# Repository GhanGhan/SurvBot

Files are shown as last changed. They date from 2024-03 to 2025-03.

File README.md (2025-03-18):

# SurvBot
Remote controlled robot that surveys the environment it is travelling in.  Designed in KiCad and Altium Designer.

# Part One - Robot Control Unit (RCU)
***Figure 1: Altium Designer 3D View***
3d View

***Figure 2: KiCad 3D View***
Full3D

## Block Diagaram
***Figure 3: SYSTEM BLOCK DIAGRAM (SIMPLE)***

Block_Diagram2

## Project Overview
- Design and implement a PCB that has closed-loop control over 2 DC motors
- Monitors and saves data about itself and the environment it is in:
  - Current flowing though the motors
  - Ambient temperature
  - Ambient light hitting the robot
  - Humidity
  - Orientation (or just the tilt angle, TBD)
- Possess Bluetooth communication
- Entire system is powered by a 9V-12V battery

***Figure 4: SYSTEM OVERVIEW***
Overview

## Schematic Diagrams
### Power
***Figure 5: Power Schematic***
Power 1
- Can be connected to a < 20V at the battery terminals, as well as 5V at either USB connector
- Schottky diodes allow for all three power sources to be connected at once
  - Battery terminal has the highest priority, followed by USB1, then USB2
  - They also provide reverse voltage protection
- Battery can power all of the modules, USB1 and USB2 power all modules except the motor control module
- U100 provides 6V with a maximum output of 3A
- U101 provides 3.3V with a maximum output of 2A
- U102 provides 3.3VA with a maximum output of 1.35A

### Microconroller
***Figure 6: Microconroller Schematic***
Microcontroller 2
- Powered by 3.3V
- Using STM32G0B1CBT6 microcontroller with a clock speed of 16MHz
- Using SWD Interface to program and debug
- Communicates to peripheral ICs using I2C, UART and SPI
- Can use PWM or PH/EN protocol to control motors
- Can connect to a host computer via the USB interface

### Motor Control
***Figure 7: Motor Control Schematic***
Motor_Control 3
- Powered by 6V
- The DRV8876 driver, one for each motor, takes control input signals form microcontroller
- Each motor driver can draw up to 1.5A before shutting down
- Each driver outputs current proportional to the current passing through its associated motor, which is converted to a voltage and sent to a voltage buffer
- Each motor has quadrature encoders, whose signals are fed to the microcontroller

### Bluetooth
***Figure 8: Bluetooth Schematic***
Bluetooth 4
- Powered by 3.3V
- Using ESP32-Mini as a UART-Bluetooth bridge to communicate with a remote controller
- Can be programmed using USB 2.0 via the USB-to-UART IC: CH340C
- By sliding a SPDT switch, can switch between programming mode and communication mode

### Sensors
***Figure 9: Sensors Schematic***
Sensors 5
- Powered by 3.3V
- Communicate with microcontroller via I2C interface
- APDS-9306-065: Ambient light sensor, automatically rejects 60Hz flicker
- SHT3D-DIS: Temperature and humidity sensor
- LSM6D53: 6-axis accelerometer and gyroscope

### Current Feedback
***Figure 10: Current Feedback Schematic***
Current_FDB 6
- Powered by 3.3VA
- Takes buffered current-sense output of left and right motor driver as input
  - Signals are filtered to attenuate switching noise before entering the buffer
- Using ADC121C02CIMK to convert analog signal to 12bit digital signal
- Communicates with microcontroller via I2C

### External Memory
***Figure 11: External Memory Schematic***
External_Memory 7
- Powered by 3.3V
- 32Mb NOR Flash memory
- Communicates with microcontroller via SPI

# Part Two - Remote Controller
***Figure 12: 3D View***
3D View Front

Battery powered hand-held device that controls and monitors the state of the SurvBot. Commands are sent and data is received over Bluetooth. The design includes joysticks to control the robot’s velocity, buttons to change the mode it is in and a screen to display the sensor data. Can be used outdoors or indoors.

## Project Overview
***Figure 13: Remote controller Bloack Diagram***
Block Diagram
The user interface will contain joysticks and buttons to control the robot’s velocity and the state it is in.   Such states will determine whether the robot responds to velocity inputs, recording sensor data, is in low power mode etc.  Velocity commands and state changes are sent from the controller to the robot via Bluetooth.  The controller will receive sensor data; encoders, temperature, humidity and motor current from the robot in and display it on the onboard screen in real time.
The system will:
- be powered by a 9V battery
- use 2 thumb joysticks, one to control the robot’s linear velocity and another to control it’s angular velocity
- provide a USB interface to to program the microcontroller
- communicate with the SurvBot over Bluetooth
- provide a screen to view the data from the SurvBot’s motion and environment sensors, and Bluetooth connection status

## Schematic Diagrams
### Power
***Figure 14: Power Schematic***
Power
- Primary power source is a rechargeable 9V battery
- Secondary power source is a USB vable
- Power multiplexing circuitry used to decide the power source
- Power Rails 3.3V and 3V (for the LCD screen)

### Microcontroller
***Figure 7: Microconroller Schematic***
uC and BT
- Programmed via a USB cable whose signals are converted to UART
- Peripherals: ADC, SPI and GPIO
- Has integrated Bluetooth antenna

### User Interface
***Figure 7: User Interface: Screen, Buttons, and Joysticks***
User Interface
- LCD screen displays information such as state of Bluetooth connection, current speed, temperature, recorded data etc.
- Features 8 buttons to control the state of the robot
- Left joysticks controls rotational speed, right joystick controls linear speed

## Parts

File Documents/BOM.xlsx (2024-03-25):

Part Name | Details/Purpose | Price | Quantity | Cost | Link | Datasheet
ROB-17279 | 2-Level, 2-wheel Robot Chassis | $16.50 | 1 | $16.50 | https://www.digikey.ca/en/products/detail/sparkfun-electronics/ROB-17279/13677596 | https://mm.digikey.com/Volume0/opasdata/d220001/medias/docus/3604/Assembly_Guide_for_SparkFun_JetBot_AI_Kit_V2.0_Web.pdf
FIT0458 | GEARMOTOR 160 RPM 6V W/ ENCODER | $7.40 | 2 | $14.80 | https://www.digikey.ca/en/products/detail/dfrobot/FIT0458/7087167 | https://mm.digikey.com/Volume0/opasdata/d220001/medias/docus/5786/FIT0458.pdf
105090004 | MAKER MDD3A - DUAL CHANNEL 3A DC (Motor Driver) | $6.90 | 1 | $6.90 | https://www.digikey.ca/en/products/detail/seeed-technology-co-ltd/105090004/10667518 | https://makermotor.com/content/cytron/pn00218-cyt12/MDD3A_Datasheet.pdf
EV3635B | Evaluation board for MC3635 Accelerometer | $14.51 | 1 | $14.51 | https://www.digikey.ca/en/products/detail/memsic-inc/EV3635B/12088270?_gl=1*ww7sy3*_up*MQ.. | https://mm.digikey.com/Volume0/opasdata/d220001/medias/docus/4034/EV3635B_User_Manual.pdf
BMP180 | DAOKI 5Pack Digital Barometric Pressure Temperature | $9.80 | 1 | $13.39 | https://www.amazon.ca/DAOKI-Digital-Barometric-Pressure-Temperature/dp/B08H4SX8ZV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
HC-SR04 | Ultrasonic Sensor Distance | $12.99 | 1 | $12.99 | https://www.amazon.ca/Organizer-Ultrasonic-Distance-MEGA2560-ElecRight/dp/B07RGB4W8V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
VEML7700 | Ambient Light Sensor | $22.99 | 1 | $22.99 | https://www.amazon.ca/HiLetgo-VEML7700-Ambient-Environment-Measuring/dp/B09KGYF83T
SHT20 | Humidity and Temperature Sensor | $15.39 | 1 | $15.39 | https://www.amazon.ca/DAOKI-Temperature-Humidity-Digital-Measurement/dp/B08XM1SS3F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

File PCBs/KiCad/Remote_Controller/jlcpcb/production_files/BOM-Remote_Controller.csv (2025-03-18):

Comment | Designator | Footprint | LCSC | Quantity
1uF | C102,C109,C110,C204,C302,C303,C304,C305,C306 | C_0402_1005Metric | C14445 | 9
100k | R103 | R_0603_1608Metric | C14675 | 1
0.1uF | C101,C106,C108,C111,C113,C202,C203,C206,C309,C310,C311,C312,C313,C314,C315,C316 | C_0402_1005Metric | C155422 | 16
USB_C_Receptacle_USB2.0_16P | J201 | USB_C_Receptacle_GCT_USB4105-xx-A_16P_TopMnt_Horizontal | C165948 | 1
5.1k | R202,R203 | R_0603_1608Metric | C23186 | 2
10k | R101,R102,R201,R204,R205,R301,R302,R303,R304,R305,R306,R307,R308 | R_0402_1005Metric | C25531 | 13
3.9uF | L101 | L_Vishay_IHLP-2525 | C257229 | 1
SW_Push | SW201 | SW_Tactile_SPST_NO_Straight_CK_PTS636Sx25SMTRLFS | C2689642 | 1
IRF7319 | Q101 | SOIC-8_3.9x4.9mm_P1.27mm | C2760082 | 1
LM74700 | U102,U104 | SOT-23-6 | C2941042 | 2
SS8050-G | Q201,Q202 | SOT-23 | C3199946 | 2
P6SMB22CA | D101 | D_SOD-882 | C320520 | 1
Power Switch | SW101,SW301,SW302,SW303,SW304,SW305,SW306,SW307,SW308 | SW_Push_1P1T_NO_CK_PTS125Sx43PSMTR | C455234 | 9
Green LED | D102 | LED_0603_1608Metric | C5252984 | 1
IRFML8244TRPBF | Q102,Q103 | SOT-23 | C5381404 | 2
22uF | C201 | C_0603_1608Metric | C59461 | 1
MCP1700T-3002E/TT | U103 | SOT-23 | C62244 | 1
ESP32-WROOM-32E | U202 | ESP32-WROOM-32D | C701341 | 1
2.2uF | C301,C307,C308 | C_0402_1005Metric | C72203 | 3
USBLC6-2SC6 | U201 | SOT-23-6 | C7519 | 1
22uF | C104,C105,C107,C112 | C_1206_3216Metric | C77091 | 4
AP63203WU | U101 | TSOT-23-6 | C780769 | 1
200R | R104 | R_0603_1608Metric | C8218 | 1
10uF | C103 | C_0805_2012Metric | C84416 | 1
CH340C | U203 | SOIC-16_3.9x9.9mm_P1.27mm | C84681 | 1
COM-09032 | JS302 | XDCR_COM-09032 |  | 1
NHD-C12832A1Z-FSW-FBW-3V3 | U301 | NHD-C12832A1Z-FSRGB |  | 1
COM-09032 | JS301 | XDCR_COM-09032 |  | 1
Battery_Cell | BT101 | BatteryHolder_MPD_BA9VPC_1xPP3 |  | 1

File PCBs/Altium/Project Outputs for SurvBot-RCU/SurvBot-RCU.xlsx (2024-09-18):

Line # | Name | Description | Designator | Quantity | Manufacturer | Manufacturer Part # | Supplier | Supplier Part # | Supplier Part Number | Supplier 1 | Manufacturer 1 | Manufacturer Part Number 1 | Manufacturer Lifecycle 1 | Supplier Part Number 1 | Supplier Unit Price 1 | Supplier Subtotal 1
 | 470uF | 470 µF 35 V Aluminum Electrolytic Capacitors Radial, Can 10000 Hrs @ 105°C | C100 | 1 | Rubycon | 35ZLH470MEFC10X16 | JLCPCB | C338196
 | 100uF | 100 µF 50 V Aluminum Electrolytic Capacitors Radial, Can 8000 Hrs @ 105°C | C101 | 1 | Rubycon | 50ZLH100MEFC8X11.5 | JLCPCB | C109393
 | 1000uF | 1000 µF 16 V Aluminum Electrolytic Capacitors Radial, Can 10000 Hrs @ 105°C | C102 | 1 | Rubycon | 16ZLH1000MEFC10X16 | JLCPCB | C338175
 | 100nF | 0.1 µF ±10% 50V Ceramic Capacitor X7R 0603 (1608 Metric) | C103, C300, C302, C303, C304, C306, C307, C401, C402, C404, C405, C407, C408, C500, C501, C503, C603, C608 | 18 | KEMET | C0603C104K5RACAUTO | JLCPCB | C129621
 | 22uF | 22 µF ±20% 10V Ceramic Capacitor X5R 0603 (1608 Metric) | C104, C105, C106, C109, C110, C409 | 6 | Samsung Electro-Mechanics | CL10A226MP8NUNE | JLCPCB | C86295
 | 1uF | 1 µF ±10% 16V Ceramic Capacitor X7R 0603 (1608 Metric) | C107, C108, C111, C112, C403, C406, C502, C700 | 8 | YAGEO | CC0603KRX7R7BB105 | JLCPCB | C106248
 | 1uF | 1 µF ±10% 16V Ceramic Capacitor X5R 0402 (1005 Metric) | C200 | 1 | Samsung Electro-Mechanics | CL05A105KO5NNNC | JLCPCB | C29266
 | 100nF | 0.1 µF ±10% 10V Ceramic Capacitor X7R 0402 (1005 Metric) | C201, C203, C205, C600, C602, C605, C607 | 7 | Samsung Electro-Mechanics | CL05B104KP5NNNC | JLCPCB | C133086
 | 4.7uF | 4.7 µF ±20% 10V Ceramic Capacitor X5R 0402 (1005 Metric) | C202 | 1 | Samsung Electro-Mechanics | CL05A475MP5NRNC | JLCPCB | Supplier Part #
 | 14pF | 50V 14pF NP0 ±5% 0402 Multilayer Ceramic Capacitors MLCC - SMD/SMT ROHS | C204, C206 | 2 | Walsin Tech Corp | 0402N140J500CT | JLCPCB | C458857
 | 22nF | 0.022 µF ±10% 100V Ceramic Capacitor X7R 0603 (1608 Metric) | C301, C305 | 2 | Murata Electronics | GCM188R72A223KA37D | JLCPCB | C161234
 | 220uF | 220 µF 35 V Aluminum Electrolytic Capacitors Radial, Can 8000 Hrs @ 105°C | C308, C309 | 2 | Rubycon | 35ZLH220MEFC8X11.5 | JLCPCB | C107639
 | 10uF | 10 µF ±20% 10V Ceramic Capacitor X5R 0603 (1608 Metric) | C400 | 1 | Murata Electronics | GRM188R61A106ME69D | JLCPCB | C90053
 | 10uF | 10 µF ±20% 10V Ceramic Capacitor X5R 0402 (1005 Metric) | C601, C606 | 2 | Murata Electronics | GRM155R61A106ME11D | JLCPCB | C408132
 | 1nF | 1000 pF ±5% 50V Ceramic Capacitor C0G, NP0 0402 (1005 Metric) | C604, C609 | 2 | Murata Electronics | GRM1555C1H102JA01D | JLCPCB | C76947
 | B340AE-13 | Diode 40 V 3A Surface Mount SMA | D100 | 1 | DIODES INCORPORATED | B340AE-13 | JLCPCB | C168859
 | SM5817PL-TP | Diode 20 V 1A Surface Mount SOD-123FL | D101, D102, D103, D104 | 4 | MCC(Micro Commercial Components) | SM5817PL-TP | JLCPCB | C669022
 | PESD3V3L1BA,115 | 26V Clamp 18A (8/20µs) Ipp Tvs Diode Surface Mount SOD-323 | D200, D202, D203, D204, D300, D301, D302, D303, D304, D305 | 10 | Nexperia | PESD3V3L1BA,115 | JLCPCB | C51450
 | USBLC6-2SC6 | Low-Capacitance ESD Protection USB | D201, D400 | 2 | STMicroelectronics
 | Green_150060GS75000 | Green 520nm LED Indication - Discrete 3.2V 0603 (1608 Metric) | D401 | 1 | Wurth Elektronik | 150060GS75000 | JLCPCB | C5252984
 | Blue_150060BS75000 | Blue 470nm LED Indication - Discrete 3.2V 0603 (1608 Metric) | D402 | 1 | Wurth Elektronik | 150060BS75000 | JLCPCB | C5197644
 | 691102710002 |  | J100 | 1 |  |  |  |  |  | Mouser | Wurth Electronics | 691102710002 | Volume Production | 710-691102710002 | 0.73 | 0.73
 | TYPE-C-31-M-12 | 5A 1 16P Female Type-C SMD USB Connectors ROHS | J200, J400 | 2 | Korean Hroparts Elec |  | JLCPCB | C165948
 | CONN 1x5 | 2.54mm 3A Single Row -40℃~+105℃ 250V 5P Direct Insert 1x5P Top Square Hole Plugin,P=2.54mm Female Headers ROHS | J201 | 1 | HanElectricity | 2541FV-5P | JLCPCB | C18723050
 | CONN 1x4 | 2.54mm 3A Single Row 4P -40℃~+105℃ 250V Direct Insert 1x4P Top Square Hole Plugin,P=2.54mm Female Headers ROHS | J300, J302 | 2 | HanElectricity | 2541FV-4P | JLCPCB | C18723049
 | WJ500V-5.08-2P | 1x2P 5.08mm 2.5 1 2 18A -40℃~+105℃ 250V Green 14~30 Direct Insert Plugin,P=5.08mm Screw Terminal Blocks ROHS | J301, J303 | 2 | Ningbo Kangnex Elec | WJ500V-5.08-2P | JLCPCB | C8465
 | 68uH | 68 µH Shielded Drum Core, Wirewound Inductor 4 A 140mOhm Max Nonstandard | L100 | 1 | Sunlord | MWSA1206S-680MT | JLCPCB | C408532
 | 15uH | 15 µH Shielded Drum Core, Wirewound Inductor 1.2 A 198mOhm Max Nonstandard | L101 | 1 | Taiyo Yuden | NRS5020T150MMGJ | JLCPCB | C222920
 | 3.9uH | 3.9 µH Shielded Drum Core, Wirewound Inductor 1.5 A 115mOhm Max Nonstandard | L102, L103 | 2 | Sunlord | SPH3015H3R9MT | JLCPCB | C431700
 | 2N7002NXAKR | N-Channel 60 V 190mA (Ta), 300mA (Tc) 265mW (Ta), 1.33W (Tc) Surface Mount TO-236AB | Q400, Q401, Q403 | 3 | Nexperia | 2N7002NXAKR | JLCPCB | C551416
 | BSS84AK,215 | P-Channel 50 V 180mA (Ta) 350mW (Ta), 1.14W (Tc) Surface Mount TO-236AB | Q402 | 1 | Nexperia | BSS84AK,215 | JLCPCB | C127273
 | 5.9K | RES 5.9K OHM 1% 100mW SMD-0603 Thick film Resistor | R100 | 1 | PANASONIC | ERJ3EKF5901V | JLCPCB | C403290
 | 1.5K | RES 1.5K OHM 1% 250mW SMD-0603 Thick film Resistor | R101 | 1 | PANASONIC | ERJPA3F1501V | JLCPCB |  | C543357
 | 5R1 | 600mW Thick Film Resistors 200V ±5% ±400ppm/℃ 5.1Ω 1206 Chip Resistor - Surface Mount | R102 | 1 | UNI-ROYAL(Uniroyal Elec) | AS0606J051JT5E | JLCPCB | C966043
 | 0R | 0 Ohms Jumper Chip Resistor 0402 (1005 Metric) Moisture Resistant Thick Film | R200 | 1 | YAGEO | RC0402JR-070RL | JLCPCB | C60485
 | 10k | 10 kOhms ±1% 0.063W, 1/16W Chip Resistor 0402 (1005 Metric) Moisture Resistant Thick Film | R201, R202, R300, R306 | 4 | YAGEO | RC0402FR-0710KL | JLCPCB | C60490
 | 49R9 | 49.9 Ohms ±1% 0.1W, 1/10W Chip Resistor 0603 (1608 Metric) Automotive AEC-Q200 Thick Film | R203, R204 | 2 | PANASONIC | ERJ3EKF49R9V | JLCPCB | C403255
 | 5.1K | 5.1 kOhms ±1% 0.1W, 1/10W Chip Resistor 0603 (1608 Metric) Moisture Resistant Thick Film | R205, R206, R401, R402 | 4 | YAGEO | RC0603FR-075K1L | JLCPCB | C105580
 | 2.2K | 2.2 kOhms ±1% 0.1W, 1/10W Chip Resistor 0603 (1608 Metric) Moisture Resistant Thick Film | R301, R307 | 2 | YAGEO | RC0603FR-072K2L | JLCPCB | C114662
 | 20K | 20 kOhms ±1% 0.1W, 1/10W Chip Resistor 0603 (1608 Metric) Automotive AEC-Q200 Thick Film | R302, R303, R308, R309 | 4 | PANASONIC | ERJ-3EKF2002V | JLCPCB | C403057
 | 40K | 40 kOhms ±0.1% 0.1W, 1/10W Chip Resistor 0603 (1608 Metric) Anti-Sulfur, Automotive AEC-Q200, Moisture Resistant Thin Film | R304, R305, R310, R311 | 4 | YAGEO | AT0603BRD0740KL | JLCPCB | C5455515
 | 10K | 10 kOhms ±1% 0.1W, 1/10W Chip Resistor 0603 (1608 Metric) Moisture Resistant Thick Film | R400, R403, R405, R406, R500 | 5 | YAGEO | RC0603FR-0710KL | JLCPCB | C98220
 | 20R | 20 Ohms ±1% 0.1W, 1/10W Chip Resistor 0603 (1608 Metric) Moisture Resistant Thick Film | R404, R407, R408 | 3 | YAGEO | RC0603FR-0720RL | JLCPCB | C125758
 | 1.6K | 1.6 kOhms ±1% 0.1W, 1/10W Chip Resistor 0603 (1608 Metric) Moisture Resistant Thick Film | R600, R602 | 2 | BOURNS | CR0603-FX-1601ELF | JLCPCB | C203329
 | 15R | 15 Ohms ±1% 0.1W, 1/10W Chip Resistor 0603 (1608 Metric) Automotive AEC-Q200 Thick Film | R601, R603 | 2 | PANASONIC | ERJ3EKF15R0V | JLCPCB | C403005
 | SPDT_JS102011JCQN | Slide Switch SPDT Surface Mount | SW | 1 | C&K | JS102011JCQN | JLCPCB | C221659
 | B3U-1000P | SWITCH TACTILE SPST-NO 0.05A 12V | SW200, SW400 | 2 | Omron Electronics | B3U-1000P | JLCPCB | C231329 |  | Newark | Omron | B3U-1000P | Volume Production | 78M0188 | 0.7 | 1.4
 | LM2576S-ADJ | Buck Switching Regulator IC Positive Adjustable 1 Output 3A TO-263-6, D2PAK (5 Leads + Tab), TO-263BA | U100 | 1 | UMW(Youtai Semiconductor Co., Ltd.) | LM2576S-ADJ | JLCPCB | C347415
 | AP63203WU-7 | Buck Switching Regulator IC Positive Fixed 3.3V 1 Output 2A SOT-23-6 Thin, TSOT-23-6 | U101 | 1 | Diodes Incorporated | AP63203WU-7 | JLCPCB | C780769
 | AZ1117ID-3.3TRG1 | Linear Voltage Regulator IC Positive Fixed 1 Output 1A TO-252-3 | U102 | 1 | Diodes Incorporated | AZ1117ID-3.3TRG1 | JLCPCB | C2926306
 | STM32G0B1CBT6 | ARM® Cortex®-M0+ STM32G0 Microcontroller IC 32-Bit Single-Core 64MHz 128KB (128K x 8) FLASH 48-LQFP (7x7) | U200 | 1 | STMicroelectronics | STM32G0B1CBT6 | JLCPCB | C2847904
 | DRV8876PWPR | DRV8876 H-Bridge Motor Driver With Integrated Current Sense and Regulation 16-HTSSOP | U300, U301 | 2 | Texas Instruments | DRV8876PWPR | JLCPCB | C575551
 | OPA320AIDBVR | General Purpose Amplifier 1 Circuit Rail-to-Rail SOT-23-5 | U300, U302, U600, U602 | 4 | Texas Instruments | OPA320AIDBVR | JLCPCB | C92494
 | CH340C | 2Mbps Transceiver USB 2.0 SOP-16 USB Converters ROHS | U400 | 1 | WCH(Jiangsu Qin Heng) | CH340C | JLCPCB | C7464026
 | ESP32-C3-MINI-1-N4 | Bluetooth, WiFi 802.11b/g/n, Bluetooth v5.0 Transceiver Module 2.412GHz ~ 2.484GHz PCB Trace Surface Mount | U401 | 1 | Espressif Systems | ESP32-C3-MINI-1-N4 | JLCPCB | C2838502
 | DG2788ADN-T1-GE4 | 2 Circuit IC Switch 2:1 500mOhm 16-miniQFN (1.8x2.6) | U402 | 1 | Vishay Intertech | DG2788ADN-T1-GE4 | JLCPCB | C222479
 | APDS-9306-065 | Optical Sensor Ambient 560nm I2C 6-SMD Module | U500 | 1 | Broadcom/AVAGO | APDS-9306-065 | JLCPCB | C2649498
 | LSM6DS3TR-C | Accelerometer, Gyroscope, Temperature, 6 Axis Sensor I2C, SPI Output | U501 | 1 | STMicroelectronics | LSM6DS3TR-C | JLCPCB | C967633
 | SHT30-DIS-B2.5KS | Humidity, Temperature 0 ~ 100% RH I2C ±2% RH 8 s Surface Mount | U502 | 1 | Sensirion | SHT30-DIS-B2.5KS | JLCPCB | C77361
 | ADC121C027CIMK/NOPB | 12 Bit Analog to Digital Converter 1 Input 1 SAR TSOT-23-6 | U601, U603 | 2 | Texas Instruments | ADC121C027CIMK/NOPB | JLCPCB | C201638
 | SST26VF032BT-104I/SM | FLASH Memory IC 32Mbit SPI - Quad I/O 104 MHz 8-SOIJ | U700 | 1 | Microchip Tech | SST26VF032BT-104I/SM | JLCPCB | C69337
 | 16MHz | 16MHz SMD crystal oscillator 12pF ±10ppm ±30ppm SMD3225-4P Crystals ROHS | Y200 | 1 | SJK(SHENZHEN CRYSTAL TECH) | 7U16000E12UCG | JLCPCB | C251610

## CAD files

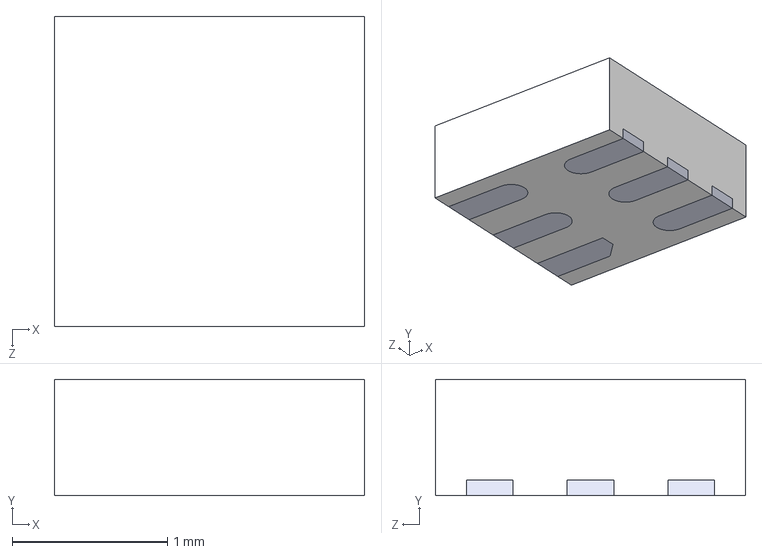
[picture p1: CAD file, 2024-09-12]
PCBs/Altium/Step_Files/APDS-9306-065--3D.STEP
2.00 x 0.75 x 2.00 mm

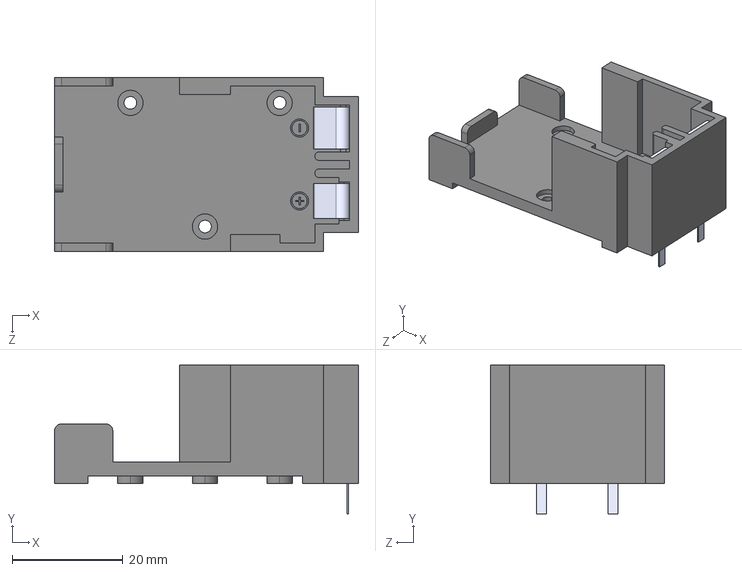
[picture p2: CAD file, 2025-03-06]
PCBs/KiCad/Project_Library/Battery_Holder/BA9VPC--3DModel-STEP-269445.STEP
54.9 x 26.9 x 31.4 mm

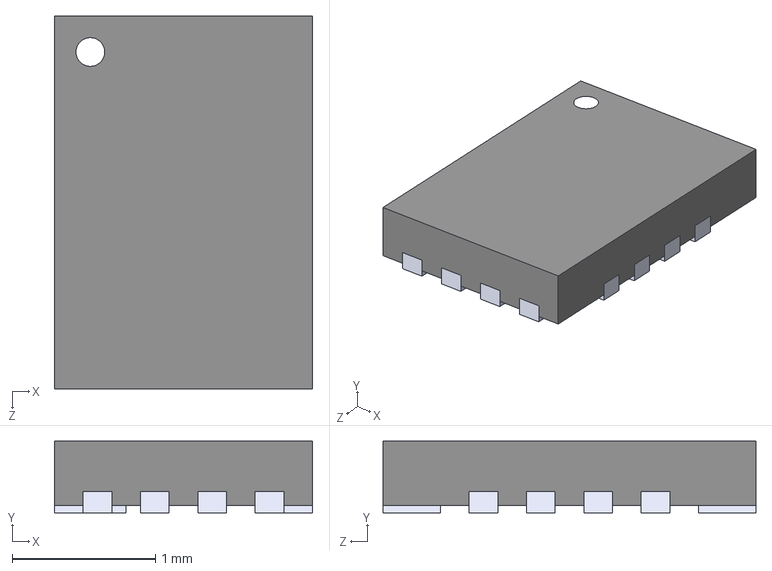
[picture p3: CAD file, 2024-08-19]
PCBs/KiCad/Project_Library/DG2788ADN-T1-GE4/FSUSB74UMX.step
1.80 x 0.5 x 2.60 mm

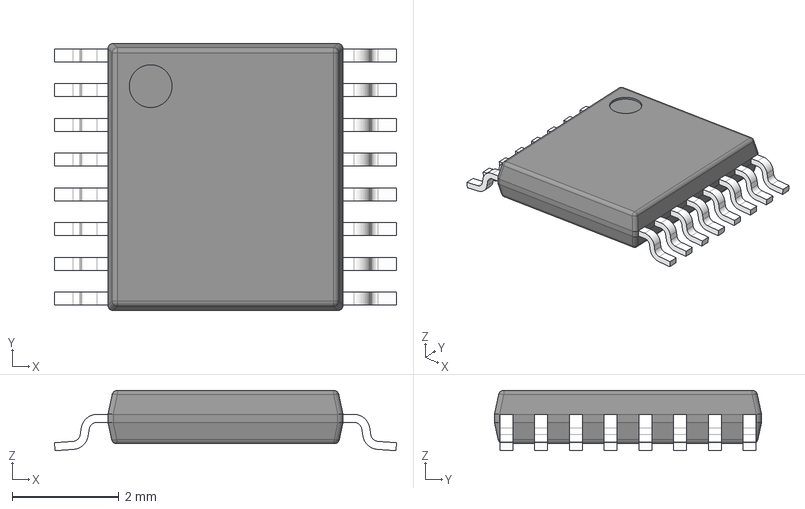
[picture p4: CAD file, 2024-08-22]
PCBs/KiCad/Project_Library/DRV8876PWP/PWP0016C.stp
6.40 x 5.00 x 1.13 mm
BODY-TSSOP
LEAD-TSSOP x 16
PIN1
DAP

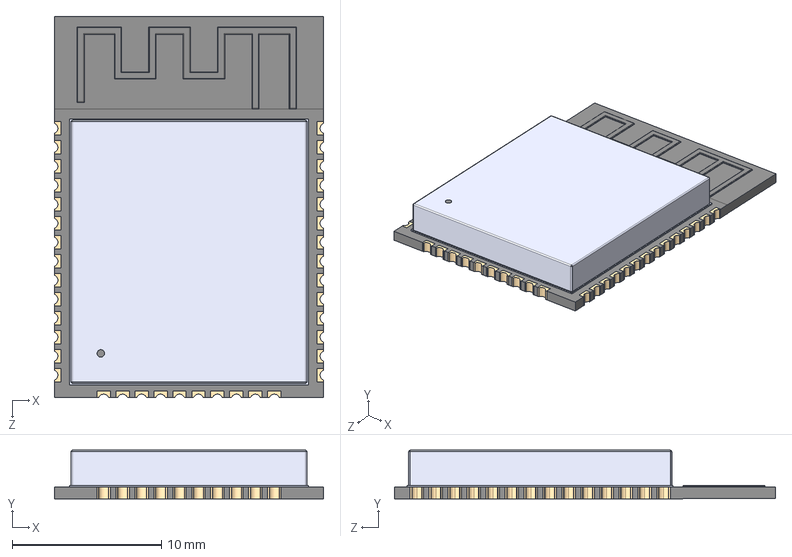
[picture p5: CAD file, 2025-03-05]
PCBs/KiCad/Project_Library/ESP32-WROOM-32E/ESP32-WROOM-32E-H4.STEP
18.0 x 3.25 x 25.5 mm

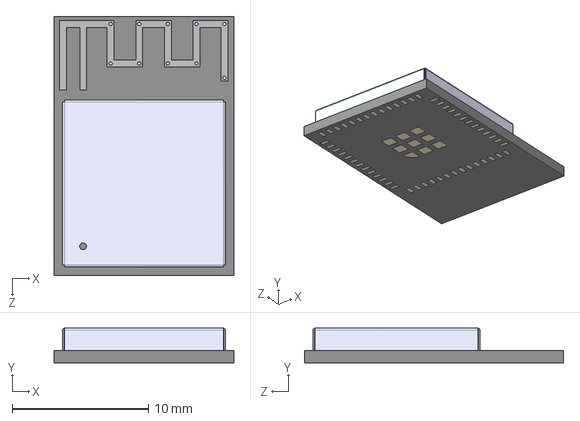
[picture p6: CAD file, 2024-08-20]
PCBs/KiCad/Project_Library/ESP32_C3_MINI_1/ESP32-MINI-1-N4.step
13.2 x 2.55 x 19.0 mm

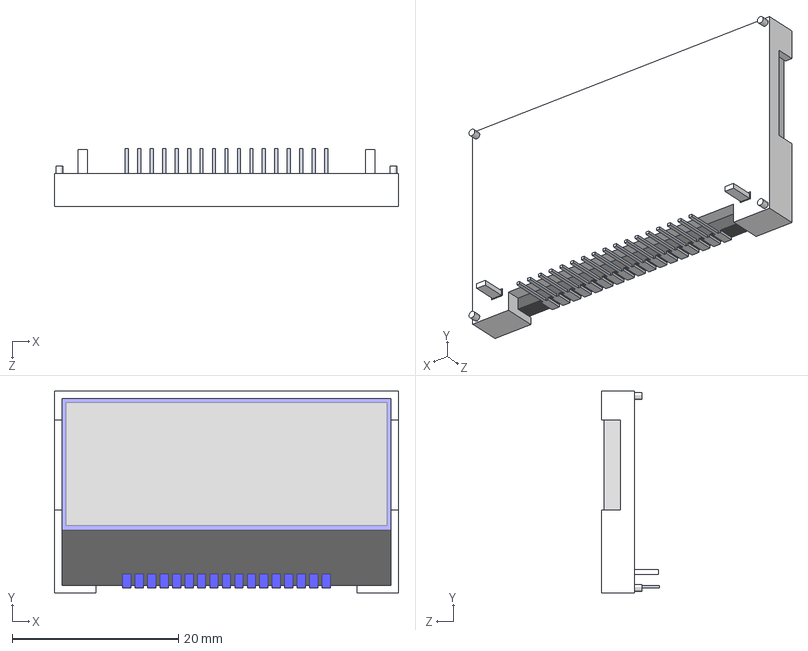
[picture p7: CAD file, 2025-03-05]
PCBs/KiCad/Project_Library/LCD_Display/NHD-C12832A1Z.STEP
41.4 x 24.3 x 7.00 mm

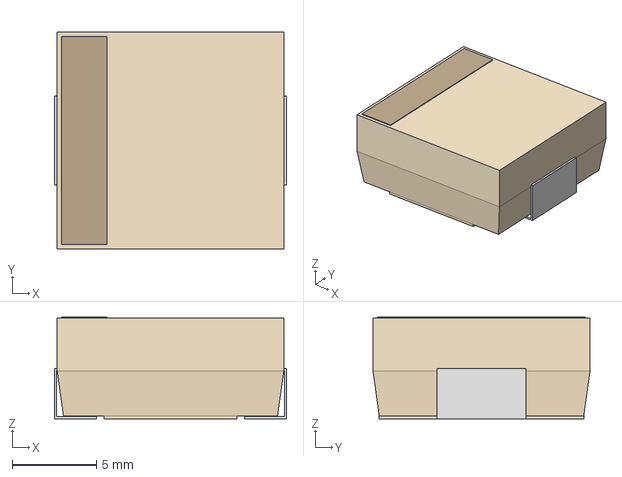
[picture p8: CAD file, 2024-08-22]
PCBs/KiCad/Project_Library/MWSA1206S-680MT/IND_MWSA1206S_SNL.step
13.8 x 12.9 x 6.04 mm

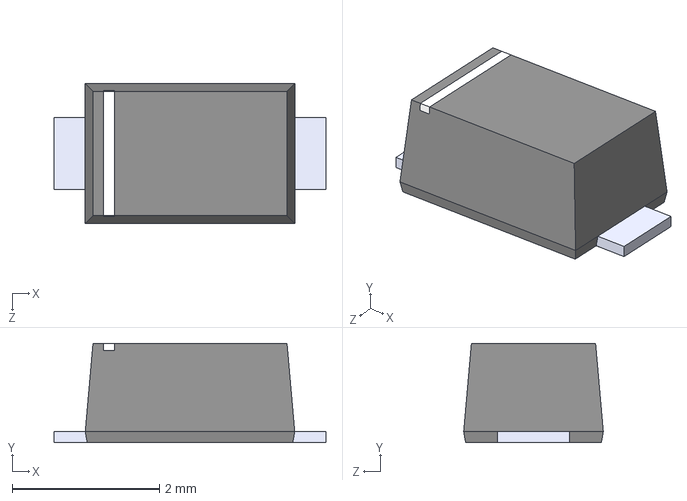
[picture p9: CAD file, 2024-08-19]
PCBs/KiCad/Project_Library/Schottky_Diode_Footprint/RS1MFL.step
3.70 x 1.35 x 1.90 mm

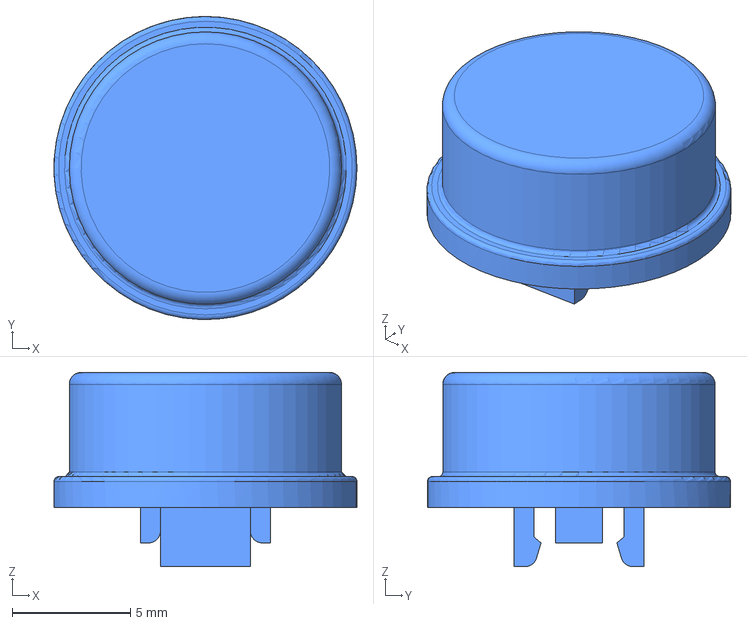
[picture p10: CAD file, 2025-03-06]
PCBs/KiCad/Project_Library/Tactile_Button/SW_Cap-A24-Blue.stp
12.8 x 12.8 x 8.20 mm

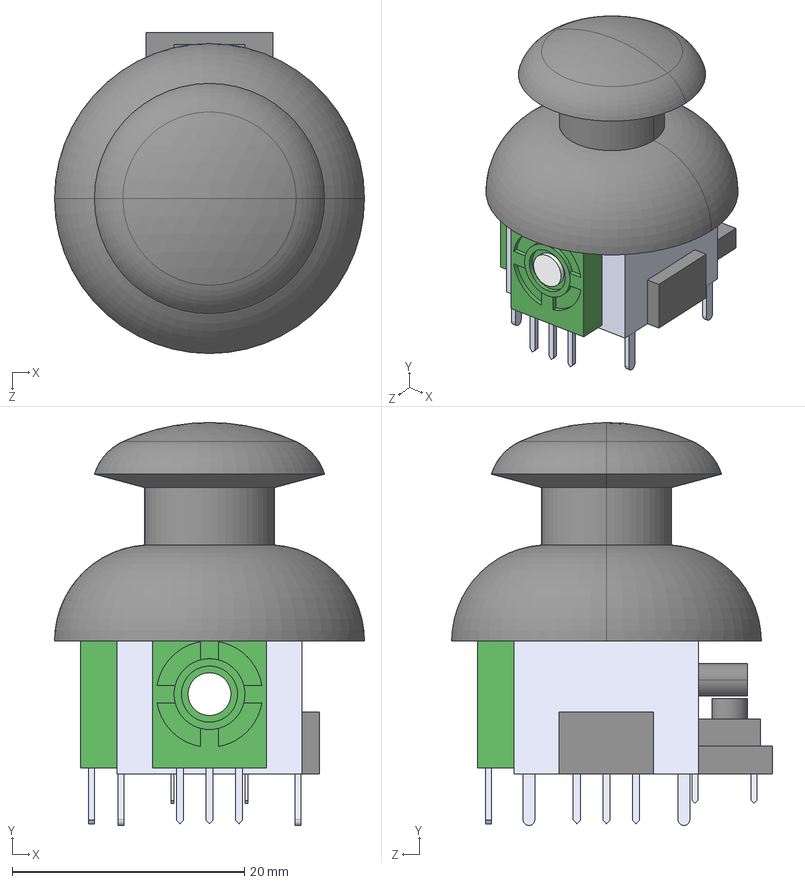
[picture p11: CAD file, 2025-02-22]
PCBs/KiCad/Project_Library/Thumb_Joystick/COM-09032.step
26.7 x 34.7 x 27.6 mm

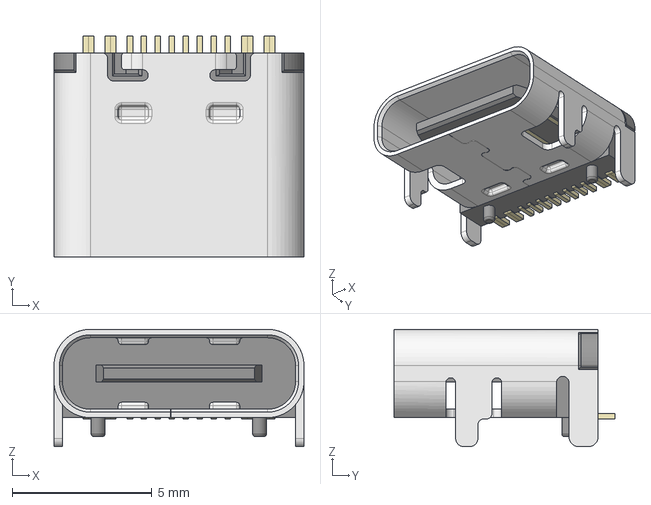
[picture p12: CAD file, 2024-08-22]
PCBs/KiCad/Project_Library/USB_3/HRO_TYPE-C-31-M-12.step
8.95 x 7.90 x 4.20 mm

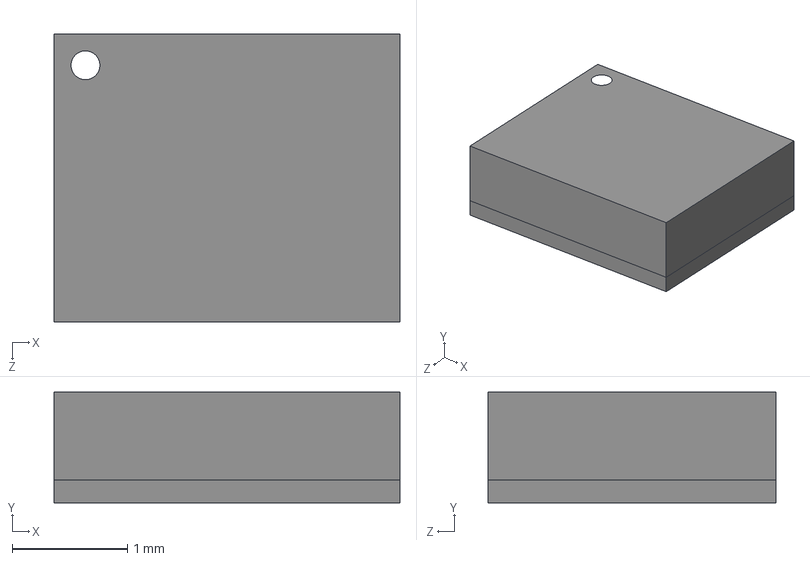
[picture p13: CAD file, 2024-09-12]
PCBs/Altium/Step_Files/LSM6DS3TR-C--3DModel.STEP
3.00 x 0.96 x 2.50 mm

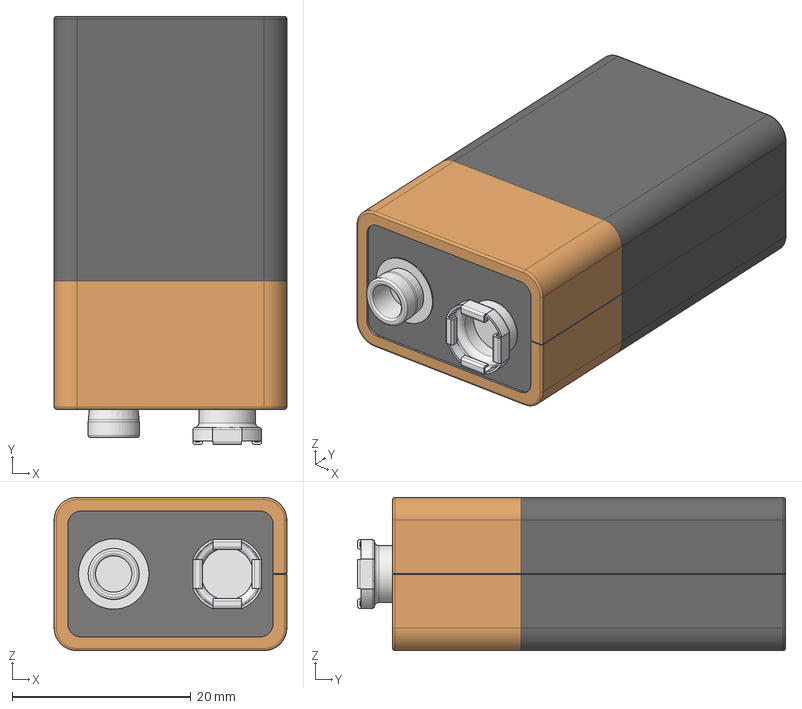
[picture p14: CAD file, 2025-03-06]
PCBs/KiCad/Project_Library/Battery_Holder/9V-battery.stp
26.0 x 47.9 x 17.1 mm

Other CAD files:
PCBs/KiCad/Project_Library/Tactile_Button/SW_Cap-A24-Green.stp
PCBs/Altium/Step_Files/ESP32-C3-MINI-1-N4--3DModel-STEP-1.STEP
PCBs/KiCad/Project_Library/Tactile_Button/SW_Cap-A24-White.stp
PCBs/Altium/Step_Files/B340AE-13.STEP
PCBs/Altium/Step_Files/CONN_4_HDR_0.1.STEP
PCBs/Altium/Step_Files/Crystal_OSC_3.2mmX2.5mm.STEP
PCBs/Altium/Step_Files/EEU-FR1V221.STEP
PCBs/Altium/Step_Files/EEUFR1A102_D10.STEP
PCBs/Altium/Step_Files/ESW-105-59-S-S.stp
PCBs/Altium/Step_Files/LED_0603.stp
PCBs/Altium/Step_Files/SM5817PL-TP.STEP
PCBs/Altium/Step_Files/Terminal_Screw_5.08mm_2P.stp
PCBs/KiCad/Project_Library/SPDTSW_JS102011JCQN/JS102011JCQN.step
PCBs/KiCad/Project_Library/Tactile_Button/Download_STP_430172073816_rev1.stp
PCBs/KiCad/Project_Library/Tactile_Button/SW_Cap-A24-Black.stp
PCBs/KiCad/Project_Library/Tactile_Button/SW_Cap-A24-Red.stp

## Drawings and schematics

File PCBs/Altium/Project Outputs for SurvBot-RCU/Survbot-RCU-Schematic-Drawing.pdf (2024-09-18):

# Altium Designer SurvBot-RCU

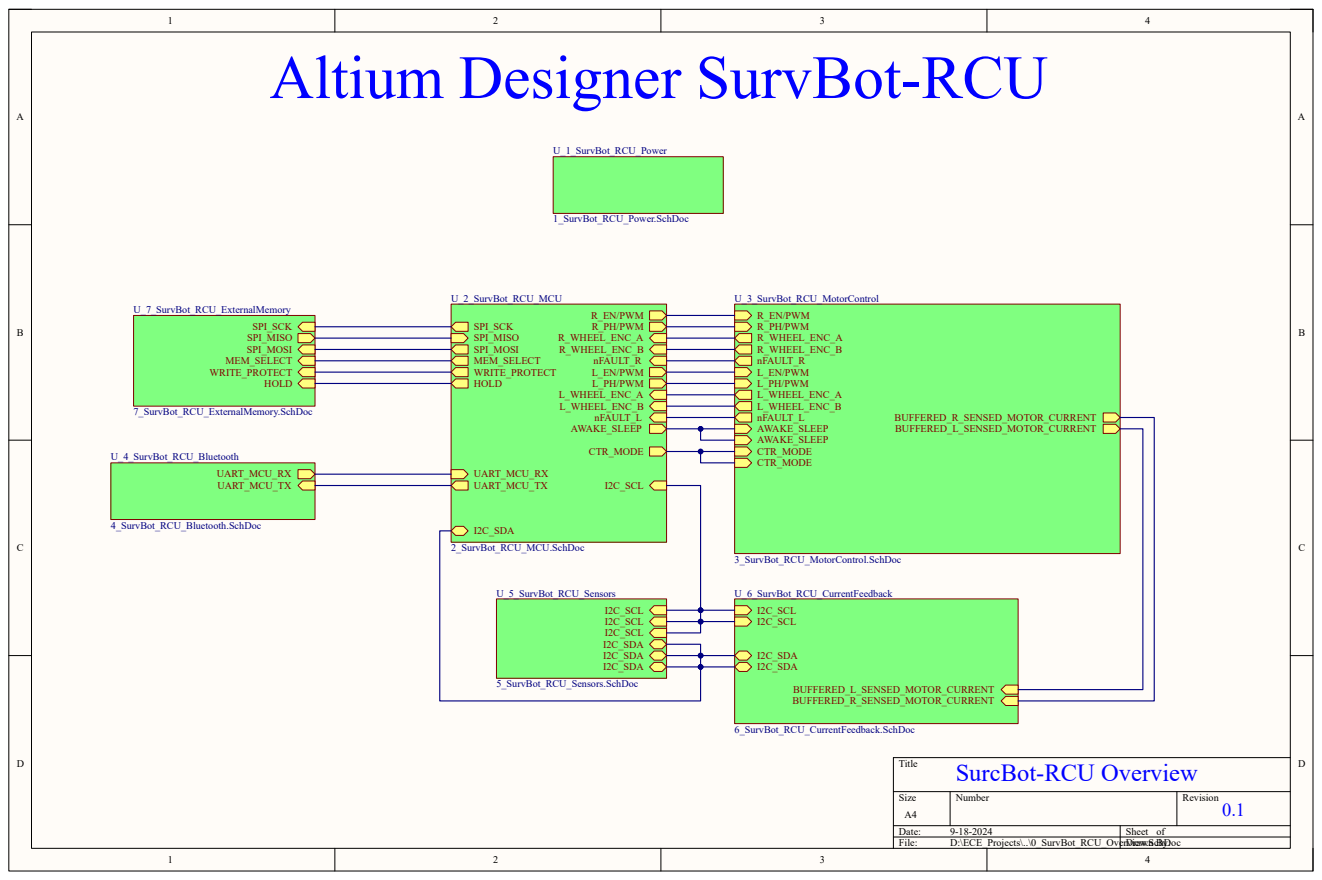
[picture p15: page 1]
Size; Number; Revision; Date:; Sheet of; File:; D:\ECE_Projects\..\0_SurvBot_RCU_Overview.SchDoc Drawn By:; U_1_SurvBot_RCU_Power; 1_SurvBot_RCU_Power.SchDoc; R_PH/PWM; R_EN/PWM; L_WHEEL_ENC_A L_WHEEL_ENC_B; L_PH/PWM; L_EN/PWM; MEM_SELECT; SPI_MOSI; SPI_MISO; SPI_SCK; WRITE_PROTECT HOLD; nFAULT_L; nFAULT_R; UART_MCU_TX; UART_MCU_RX; CTR_MODE; AWAKE_SLEEP; R_WHEEL_ENC_A R_WHEEL_ENC_B; I2C_SDA; I2C_SCL; U_2_SurvBot_RCU_MCU; 2_SurvBot_RCU_MCU.SchDoc; R_EN/PWM R_PH/PWM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

Title
SurcBot-RCU Overview

# Battery Connector Powers Motor Control [3]

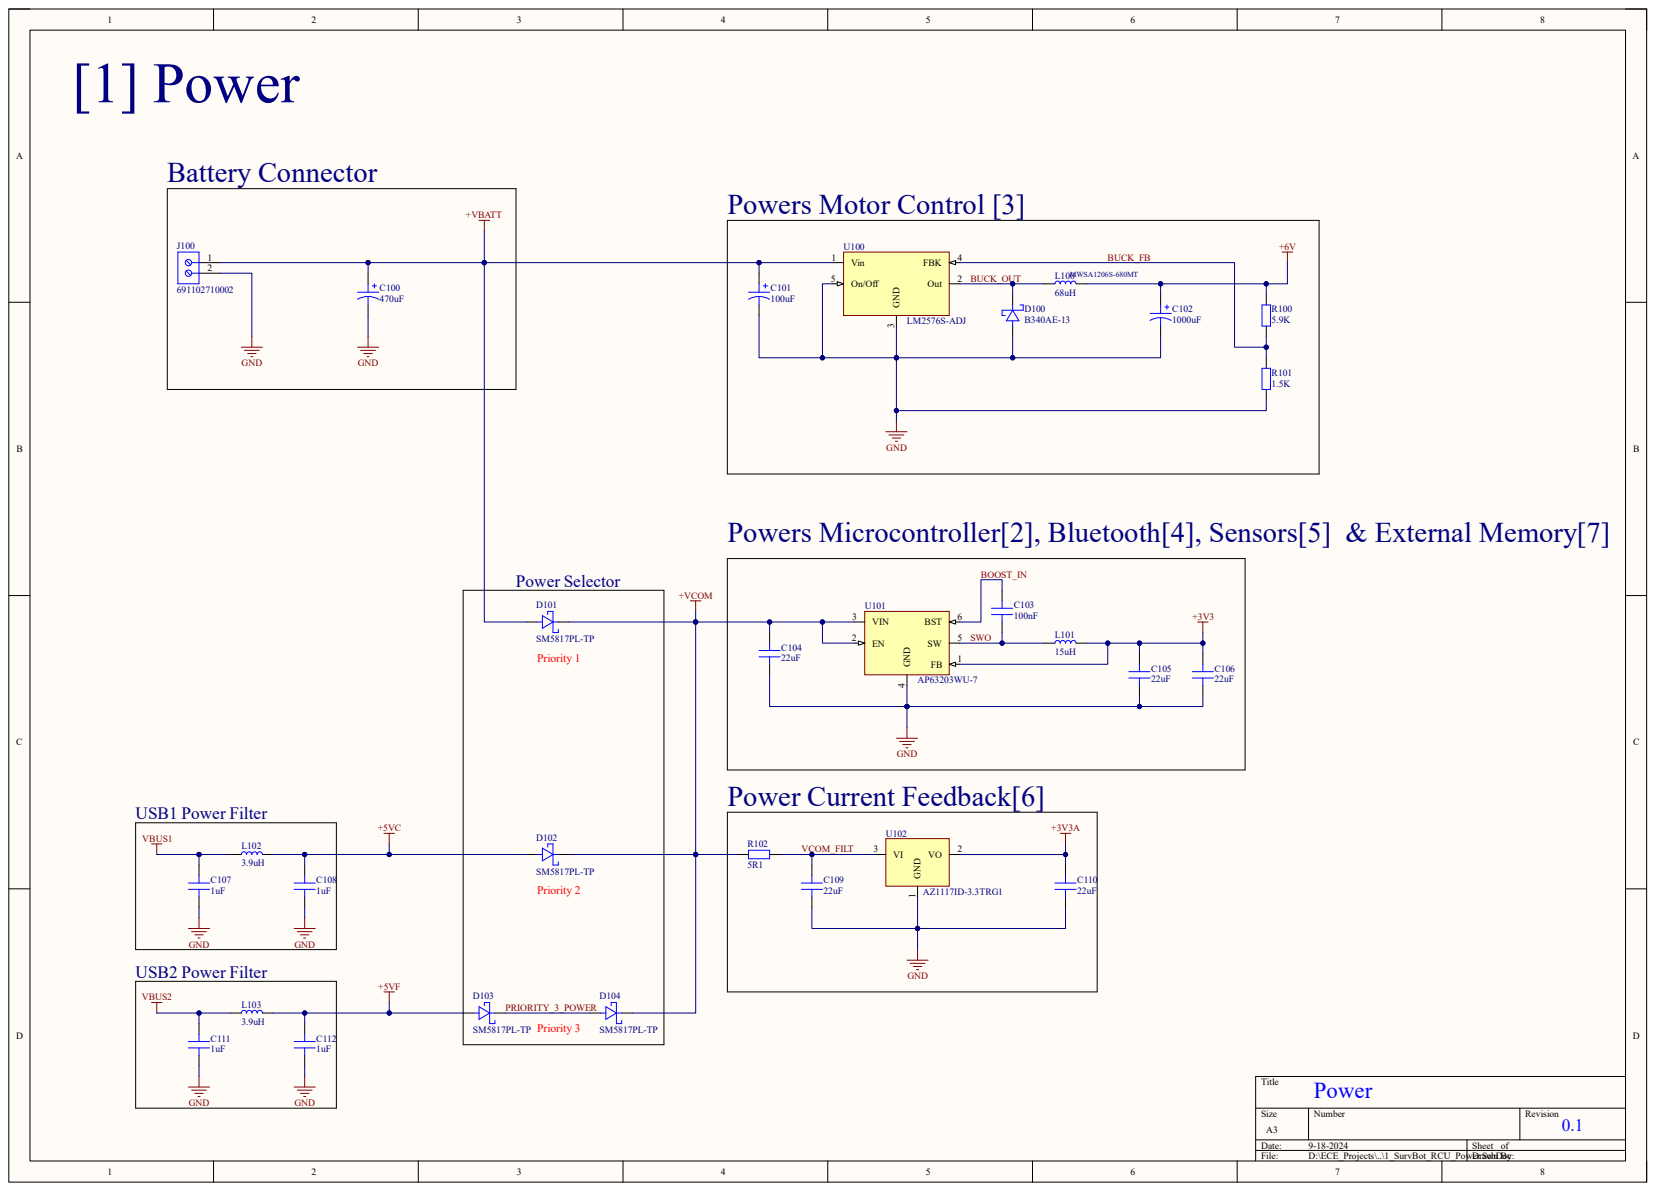
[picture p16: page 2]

Powers Microcontroller[2], Bluetooth[4], Sensors[5] & External Memory[7]

# MCU (STM32G0B1CBT6)

# [2] MCU

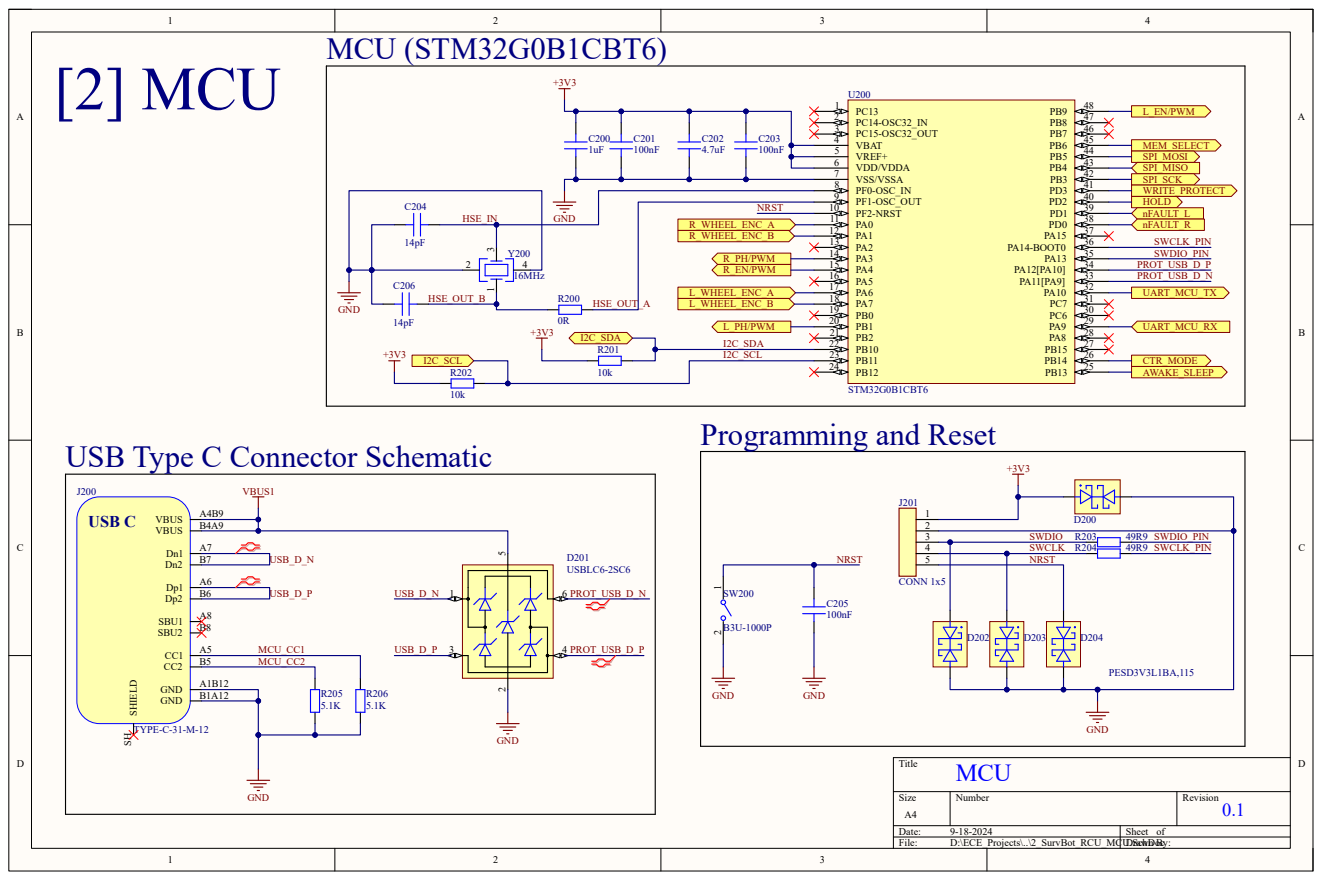
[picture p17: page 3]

USB Type C Connector Schematic

# Right Motor Drive Unit Right Motor Current Sensing

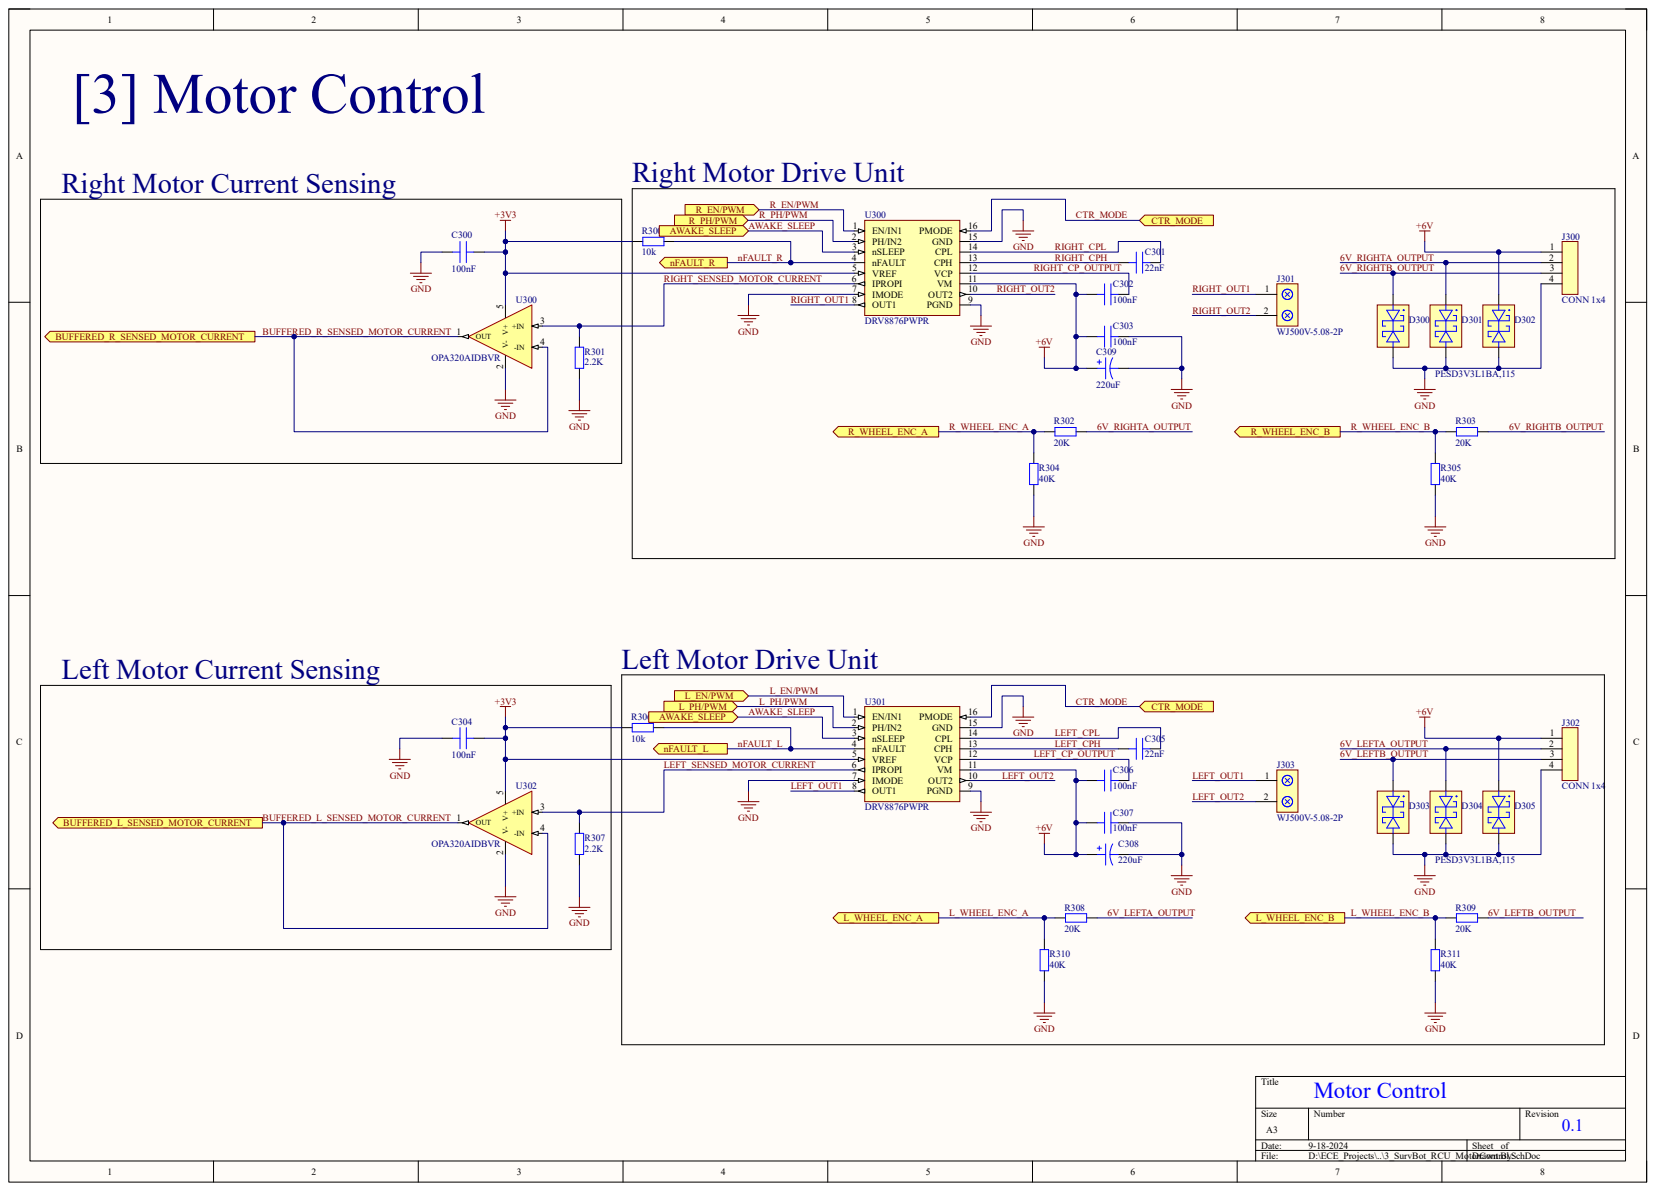
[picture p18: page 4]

Left Motor Drive Unit

Left Motor Current Sensing

## USB Type C Connector Schematic

## USB to UART with CH340C

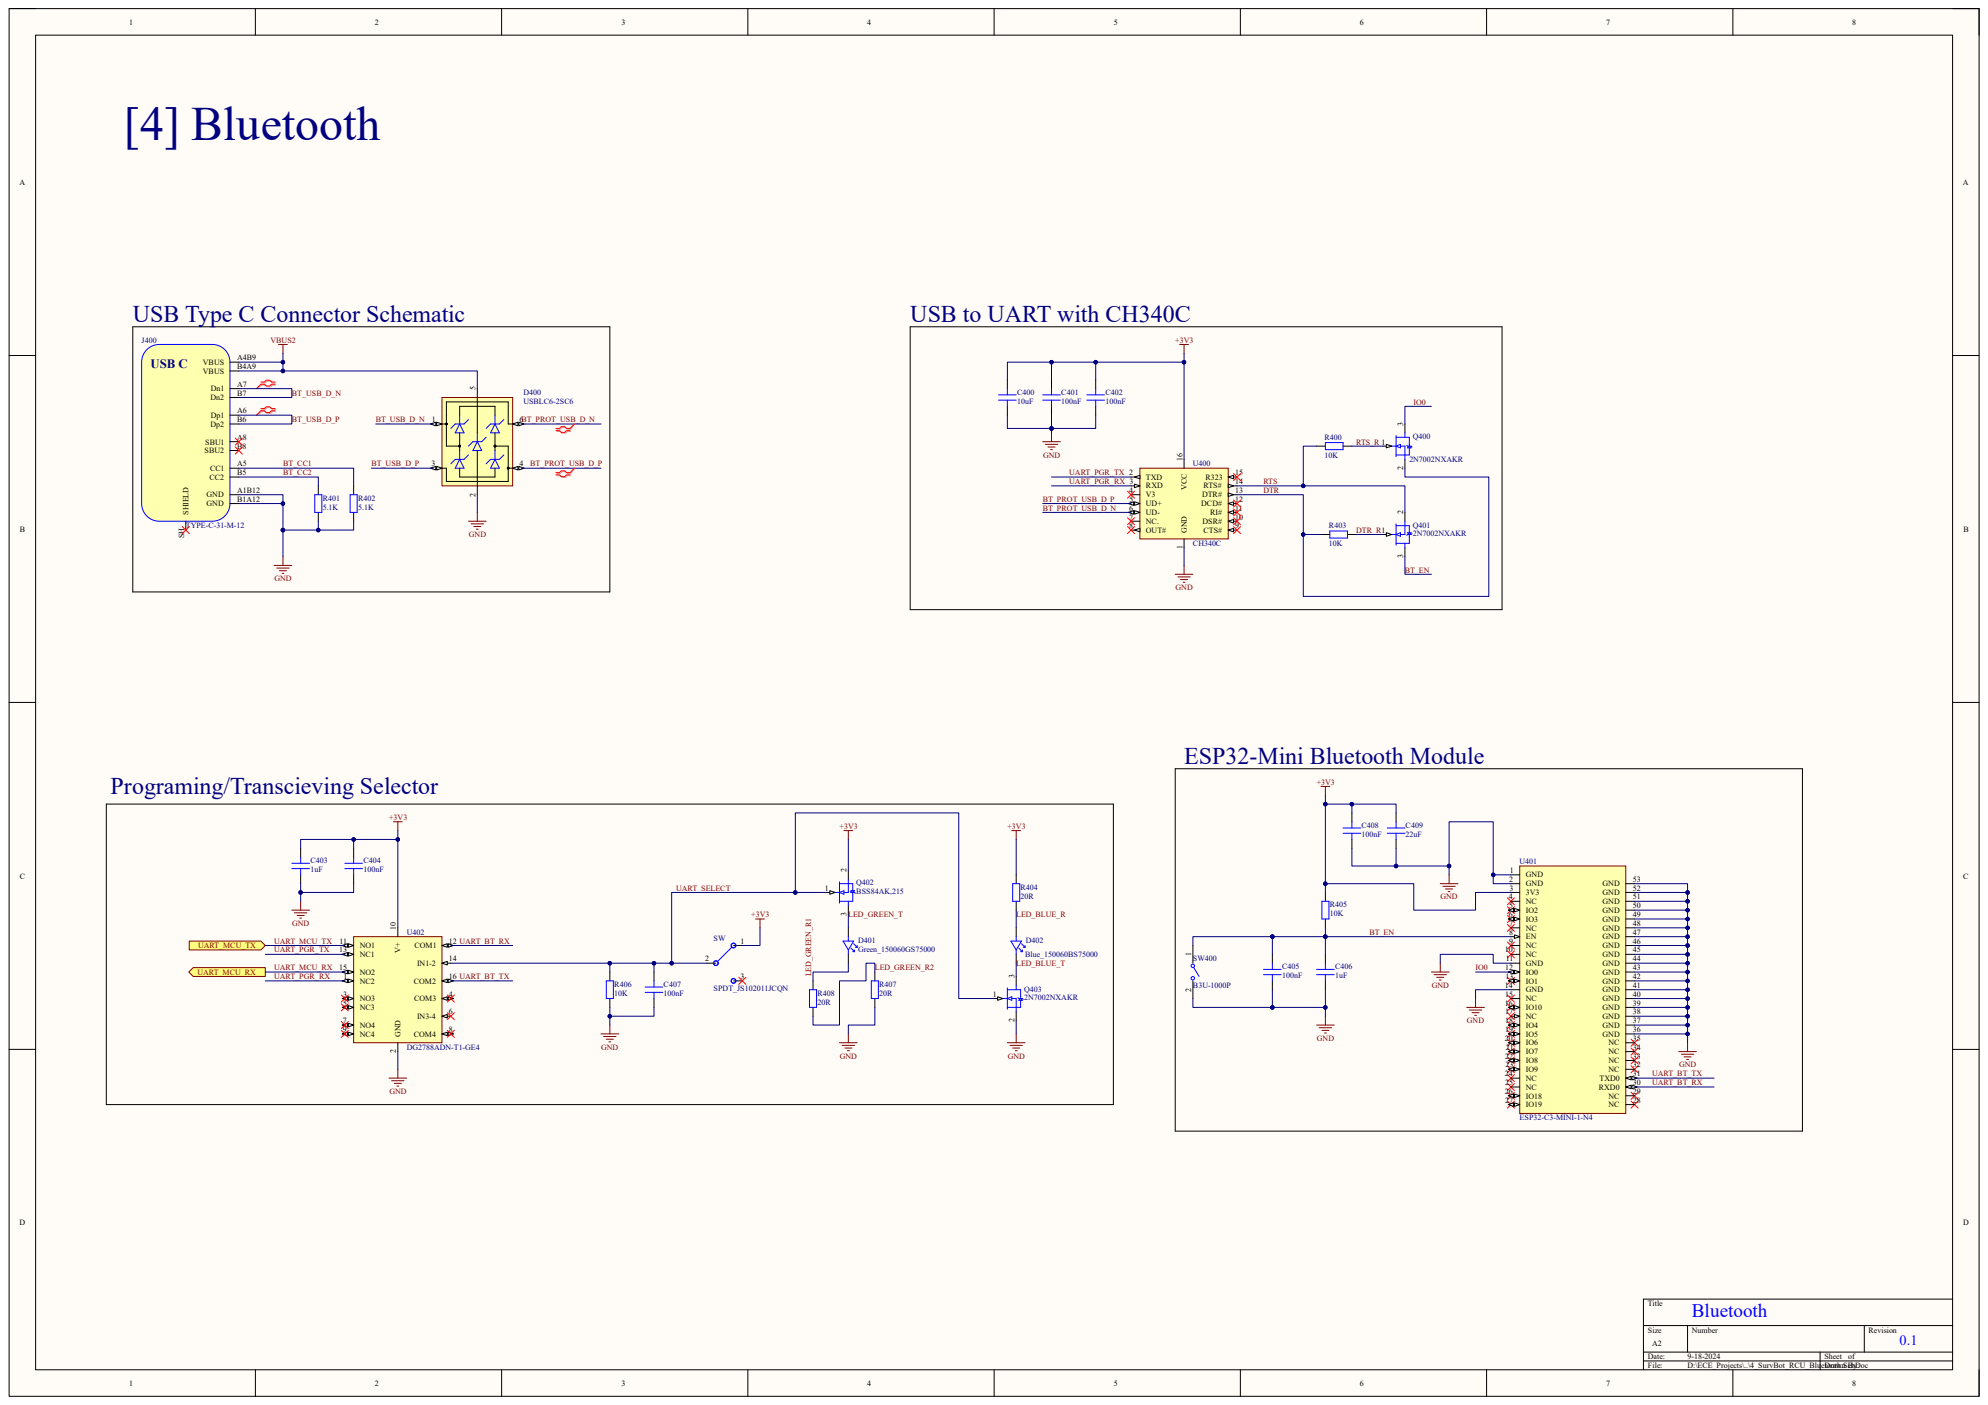
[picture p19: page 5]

# Ambient Light Sensor

# Accelerometer & Gyroscope

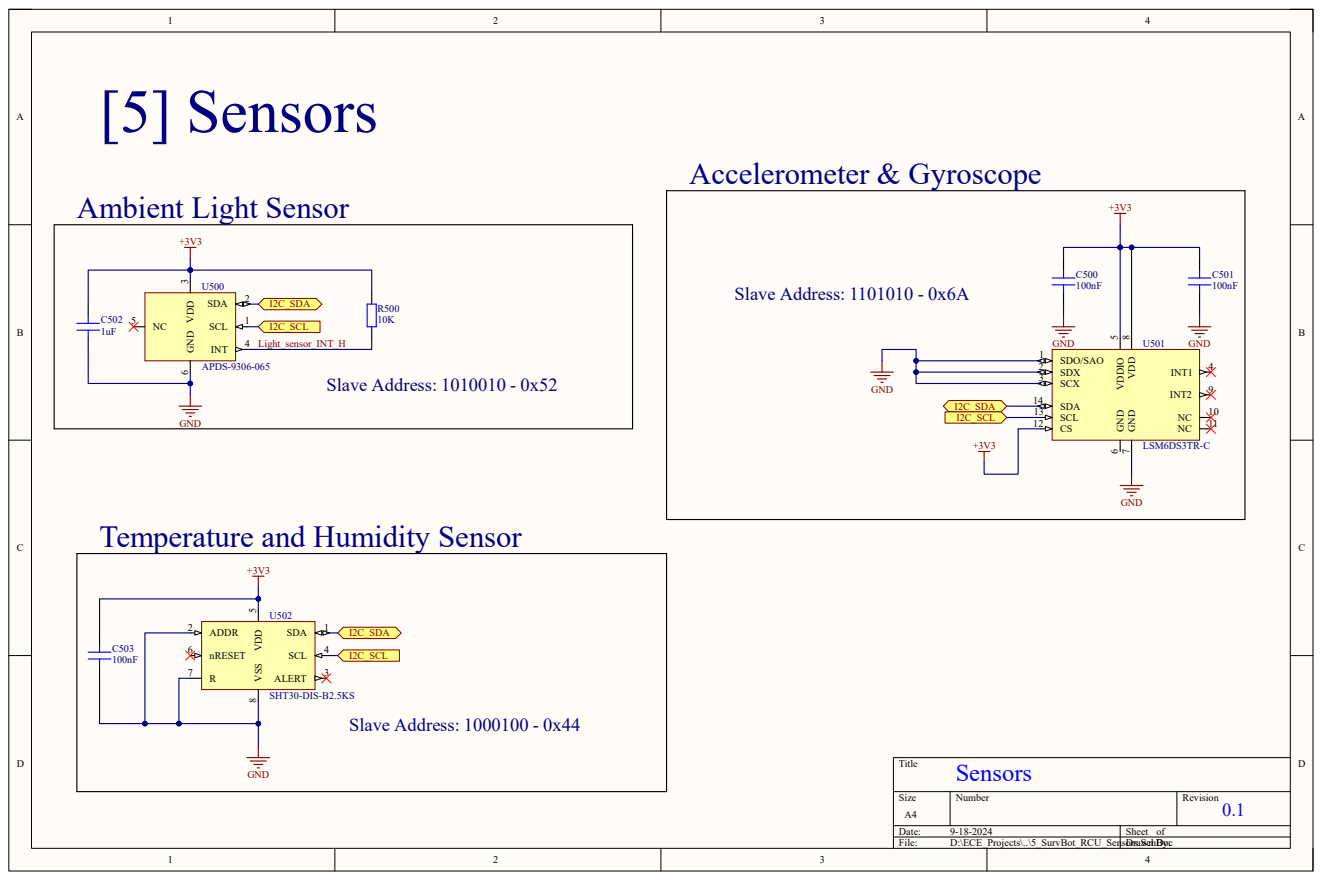
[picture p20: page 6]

Temperature and Humidity Sensor

# [6] Current Feedback

# Right Motor Current ADC

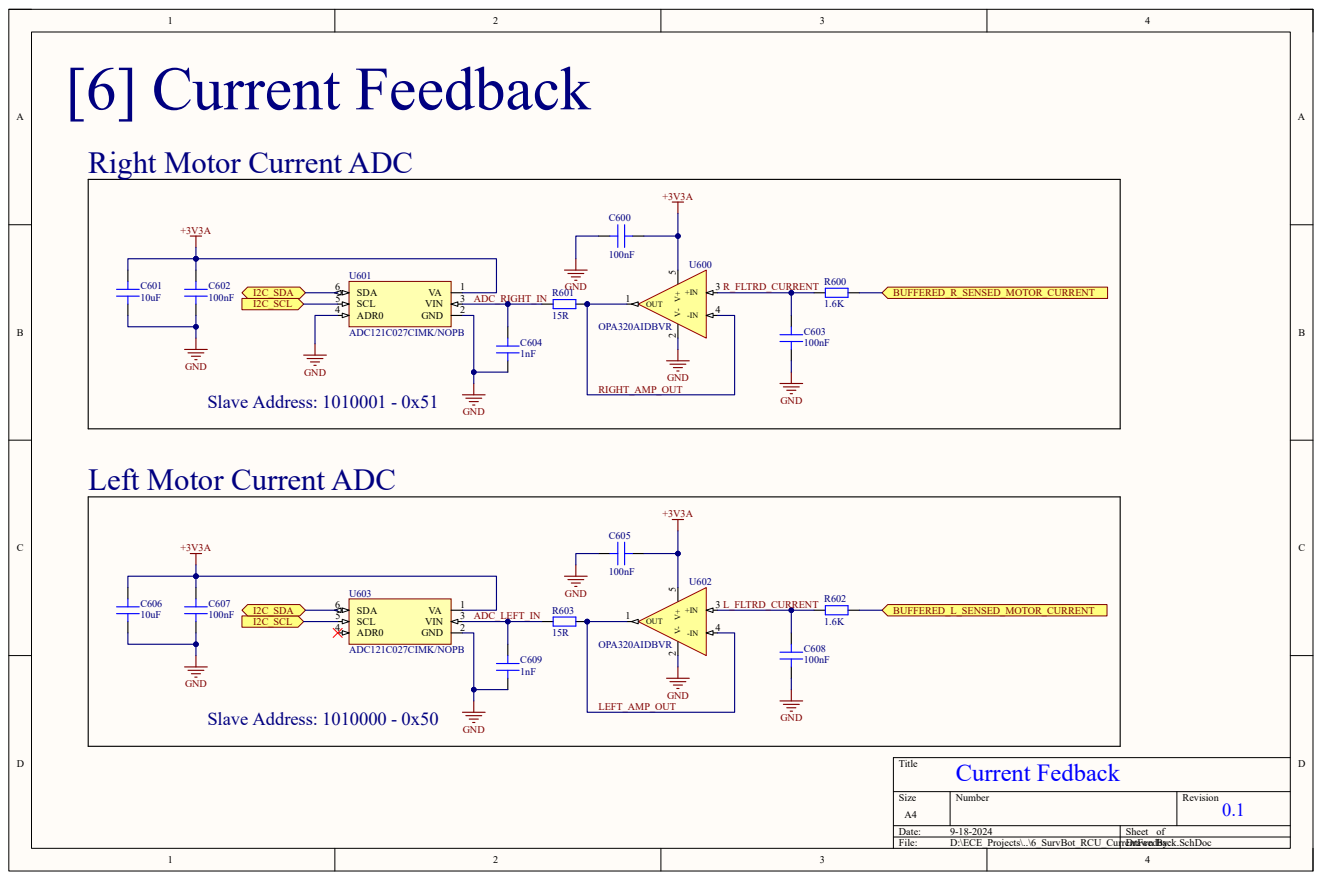
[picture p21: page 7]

Left Motor Current ADC

# [7] External Memory

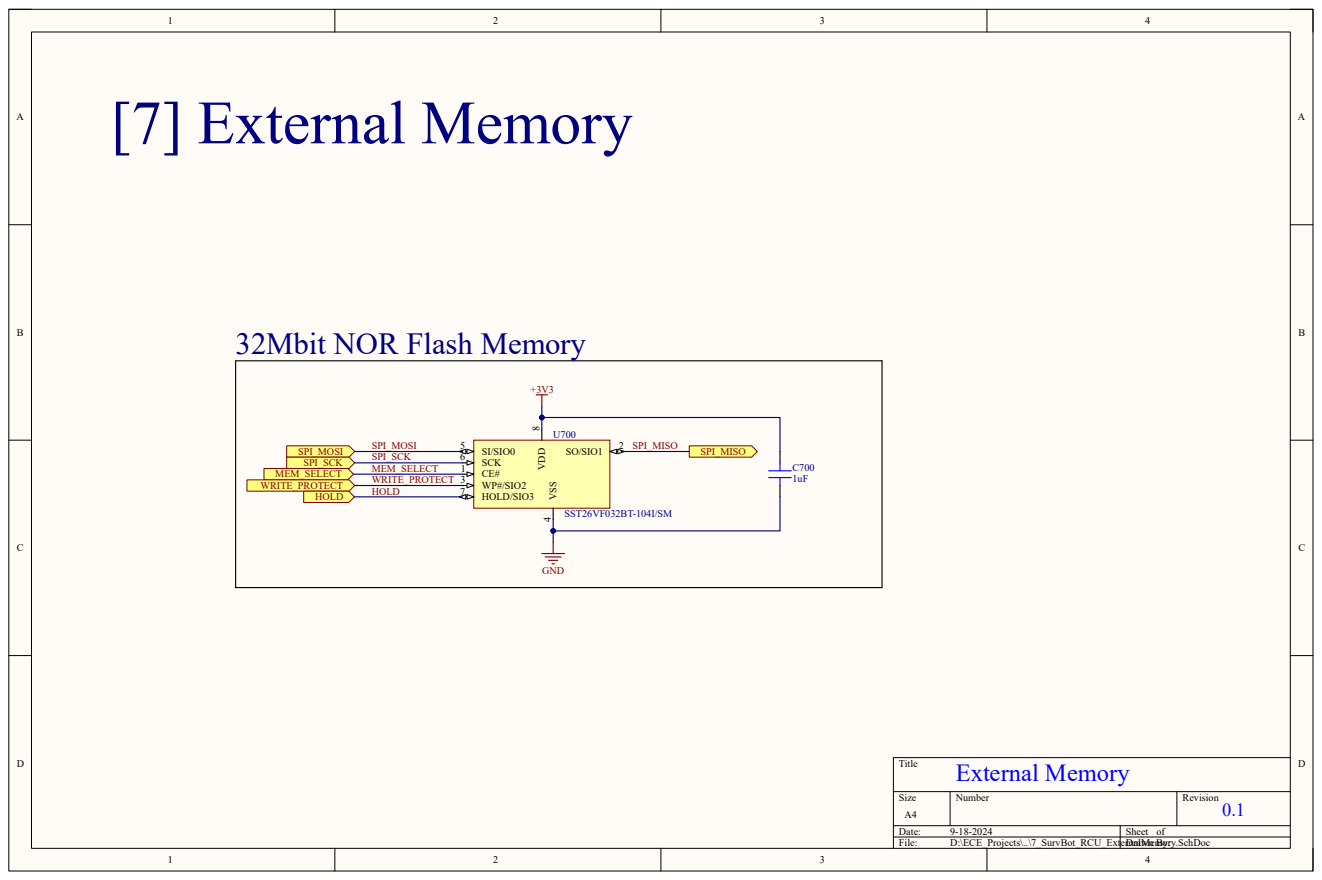
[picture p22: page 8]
Title; Size; Number; Revision; File:; D:\ECE_Projects\..\7_SurvBot_RCU_ExternalMemory.SchDoc Drawn By:; GND; SO/SIO1; WP#/SIO2 3; VSS; SI/SIO0 5 SCK 6; HOLD/SIO3 7; VDD; SST26VF032BT-104I/SM; MEM_SELECT; SPI_MOSI; SPI_MISO; SPI_SCK; WRITE_PROTECT HOLD; WRITE_PROTECT; HOLD; External Memory

32Mbit NOR Flash Memory

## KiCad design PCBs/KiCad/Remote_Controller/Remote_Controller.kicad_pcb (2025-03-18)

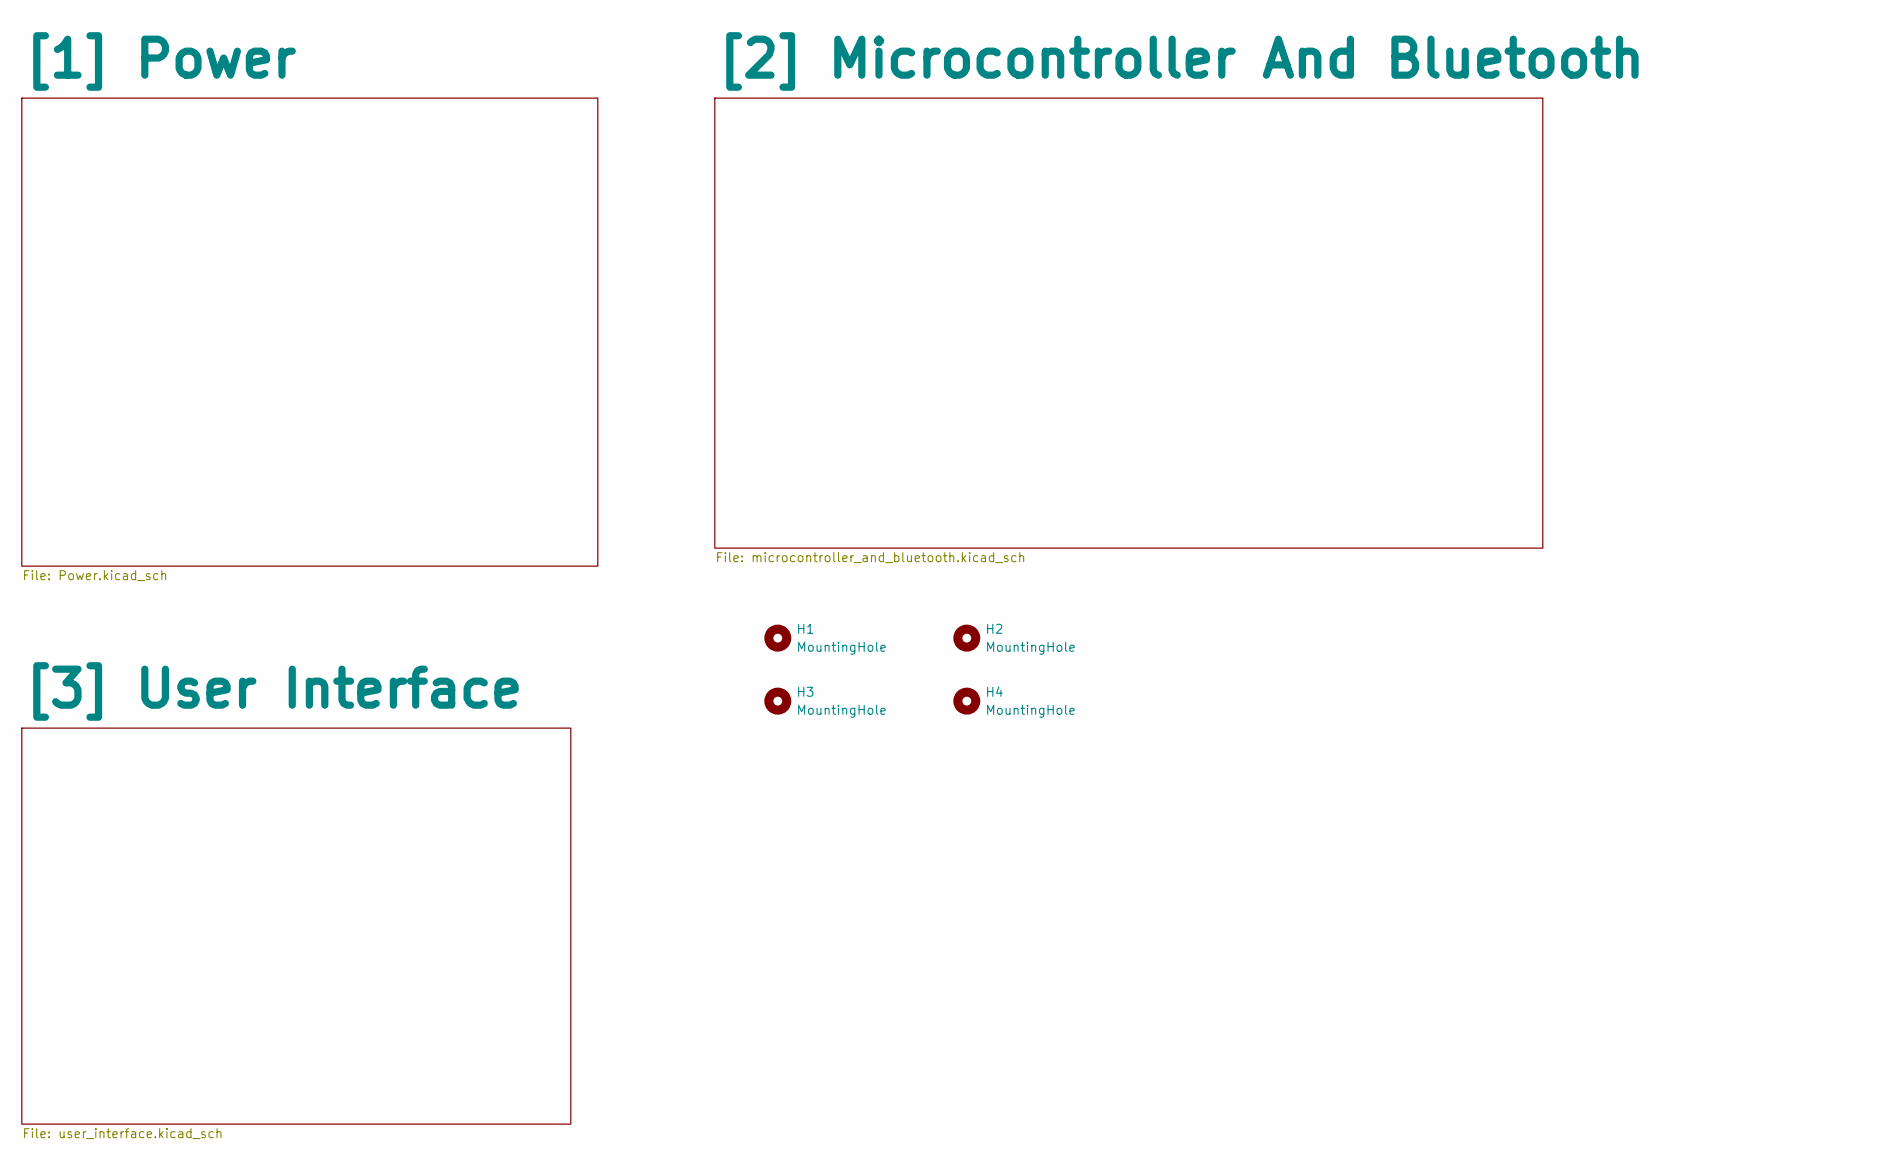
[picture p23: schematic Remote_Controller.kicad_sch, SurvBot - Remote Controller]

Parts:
H1, H2, H3, H4: MountingHole; MountingHole_2mm

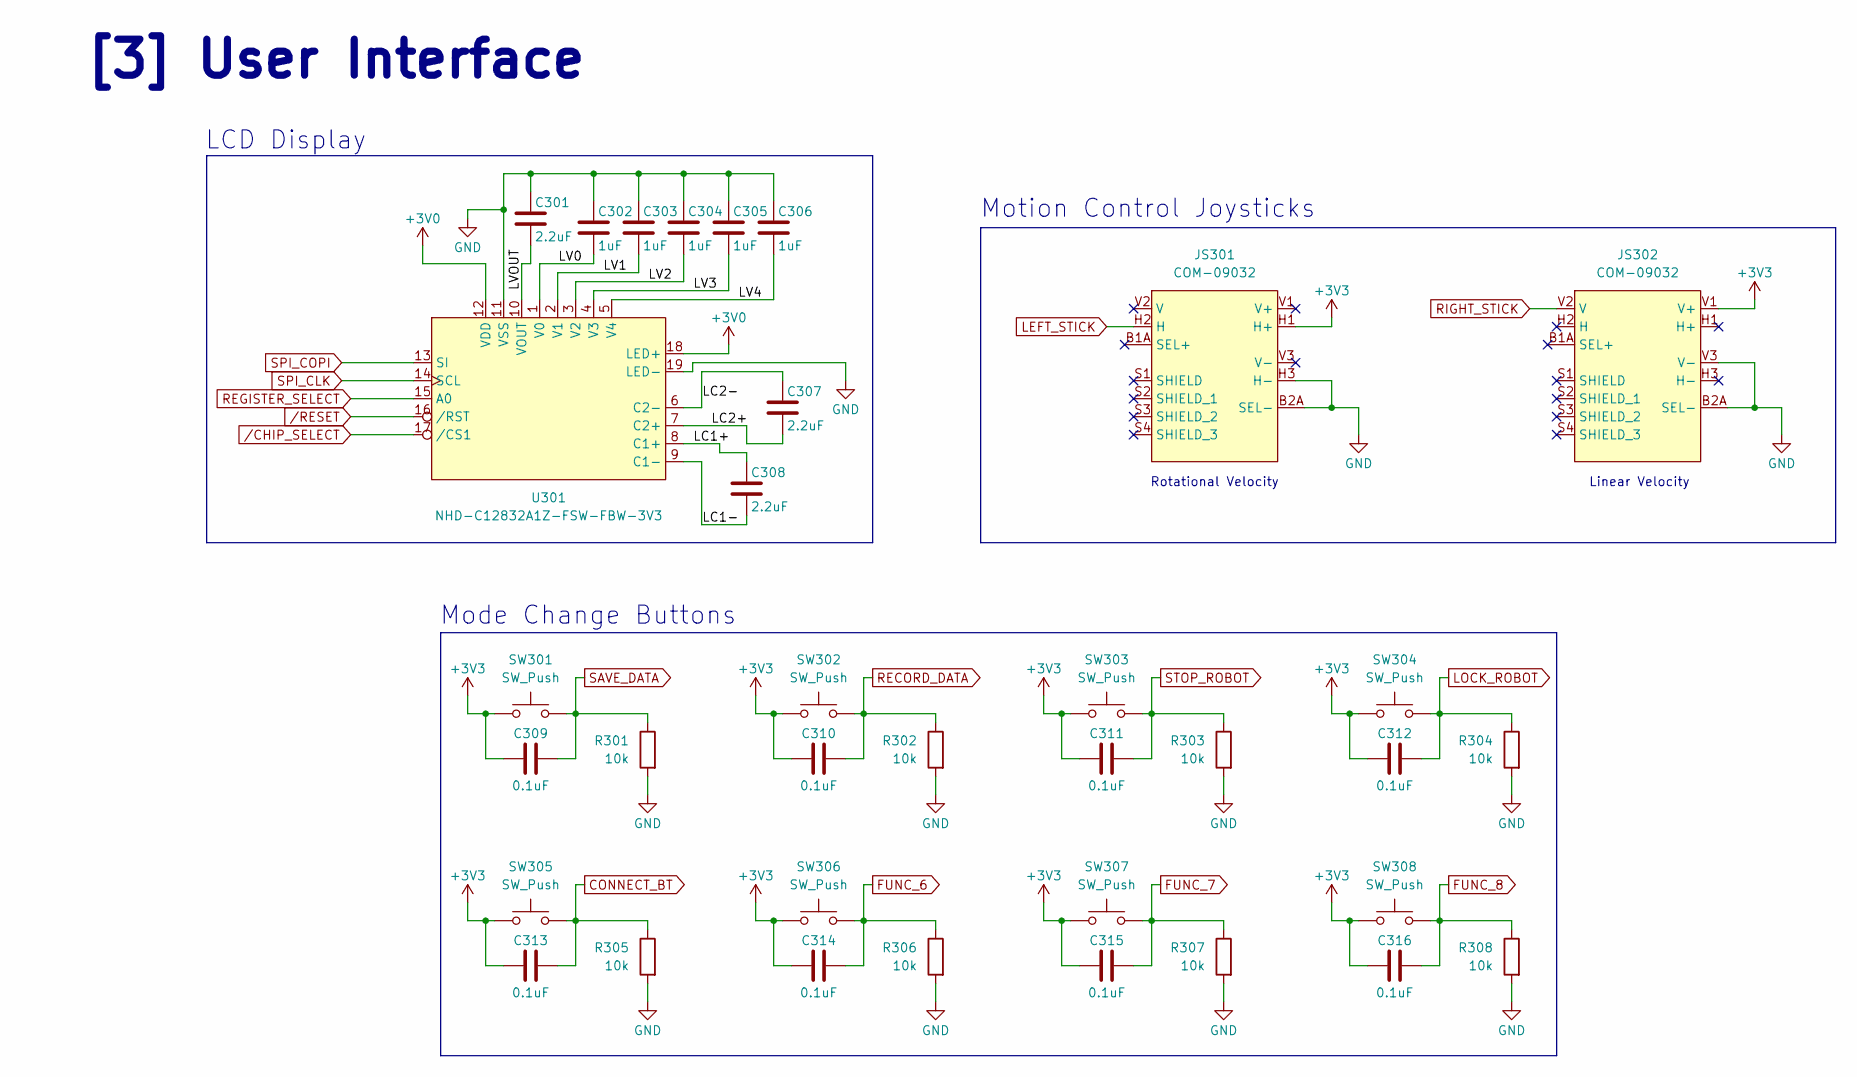
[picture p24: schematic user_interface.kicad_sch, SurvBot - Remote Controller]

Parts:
C301, C307, C308: 2.2uF; C_0402_1005Metric; Manufacturer Part # GRM155R61E225ME15D; JLCPCB Part # C72203
C302, C303, C304, C305, C306: 1uF; C_0402_1005Metric; Manufacturer Part # CL05A105KP5NNNC; JLCPCB Part # C14445
C309, C310, C311, C312, C313, C314, C315, C316: 0.1uF; C_0402_1005Metric; Manufacturer Part # CL05B104KA5NNNC; JLCPCB Part # C155422
JS301, JS302: COM-09032; XDCR_COM-09032; Manufacturer Part # COM-09032
R301, R302, R303, R304, R305, R306, R307, R308: 10k; R_0402_1005Metric; Manufacturer Part # 0402WGJ0103TCE; JLCPCB Part # C25531
SW301, SW302, SW303, SW304, SW305, SW306, SW307, SW308: SW_Push; SW_Push_1P1T_NO_CK_PTS125Sx43PSMTR; Manufacturer Part # TS-1003ST-26; JLCPCB Part # C455234
U301: NHD-C12832A1Z-FSW-FBW-3V3; NHD-C12832A1Z-FSRGB; Manufacturer Part # NHD-C12832A1Z-FSW-FBW-3V3

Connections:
+3V0: U301.12 (VDD), U301.18 (LED+); also elsewhere on the board
+3V3: C309.2, C310.2, C311.2, C312.2, C313.2, C314.2, C315.2, C316.2, JS301.H1 (H+), JS302.V1 (V+), SW301.2, SW302.2, SW303.2, SW304.2, SW305.2, SW306.2, SW307.2, SW308.2; also elsewhere on the board
/[3] User Interface/LC1+: C308.1, U301.8 (C1+)
/[3] User Interface/LC1-: C308.2, U301.9 (C1-)
/[3] User Interface/LC2+: C307.2, U301.7 (C2+)
/[3] User Interface/LC2-: C307.1, U301.6 (C2-)
/[3] User Interface/LV0: C302.2, U301.1 (V0)
/[3] User Interface/LV1: C303.2, U301.2 (V1)
/[3] User Interface/LV2: C304.2, U301.3 (V2)
/[3] User Interface/LV3: C305.2, U301.4 (V3)
/[3] User Interface/LV4: C306.2, U301.5 (V4)
/[3] User Interface/LVOUT: C301.2, U301.10 (VOUT)
CONNECT_BT: C313.1, R305.1, SW305.1; also elsewhere on the board
FUNC_6: C314.1, R306.1, SW306.1; also elsewhere on the board
FUNC_7: C315.1, R307.1, SW307.1; also elsewhere on the board
FUNC_8: C316.1, R308.1, SW308.1; also elsewhere on the board
GND: C301.1, C302.1, C303.1, C304.1, C305.1, C306.1, JS301.B2A (SEL-), JS301.H3 (H-), JS302.B2A (SEL-), JS302.V3 (V-), R301.2, R302.2, R303.2, R304.2, R305.2, R306.2, R307.2, R308.2, U301.11 (VSS), U301.19 (LED-); also elsewhere on the board
LEFT_STICK: JS301.H2 (H); also elsewhere on the board
LOCK_ROBOT: C312.1, R304.1, SW304.1; also elsewhere on the board
RECORD_DATA: C310.1, R302.1, SW302.1; also elsewhere on the board
REGISTER_SELECT: U301.15 (A0); also elsewhere on the board
RIGHT_STICK: JS302.V2 (V); also elsewhere on the board
SAVE_DATA: C309.1, R301.1, SW301.1; also elsewhere on the board
SPI_CLK: U301.14 (SCL); also elsewhere on the board
SPI_COPI: U301.13 (SI); also elsewhere on the board
STOP_ROBOT: C311.1, R303.1, SW303.1; also elsewhere on the board
/CHIP_SELECT: U301.17 (/CS1); also elsewhere on the board
/RESET: U301.16 (/RST); also elsewhere on the board

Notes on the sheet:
Mode Change Buttons
LCD Display
Rotational Velocity
Linear Velocity
Motion Control Joysticks
[3] User Interface

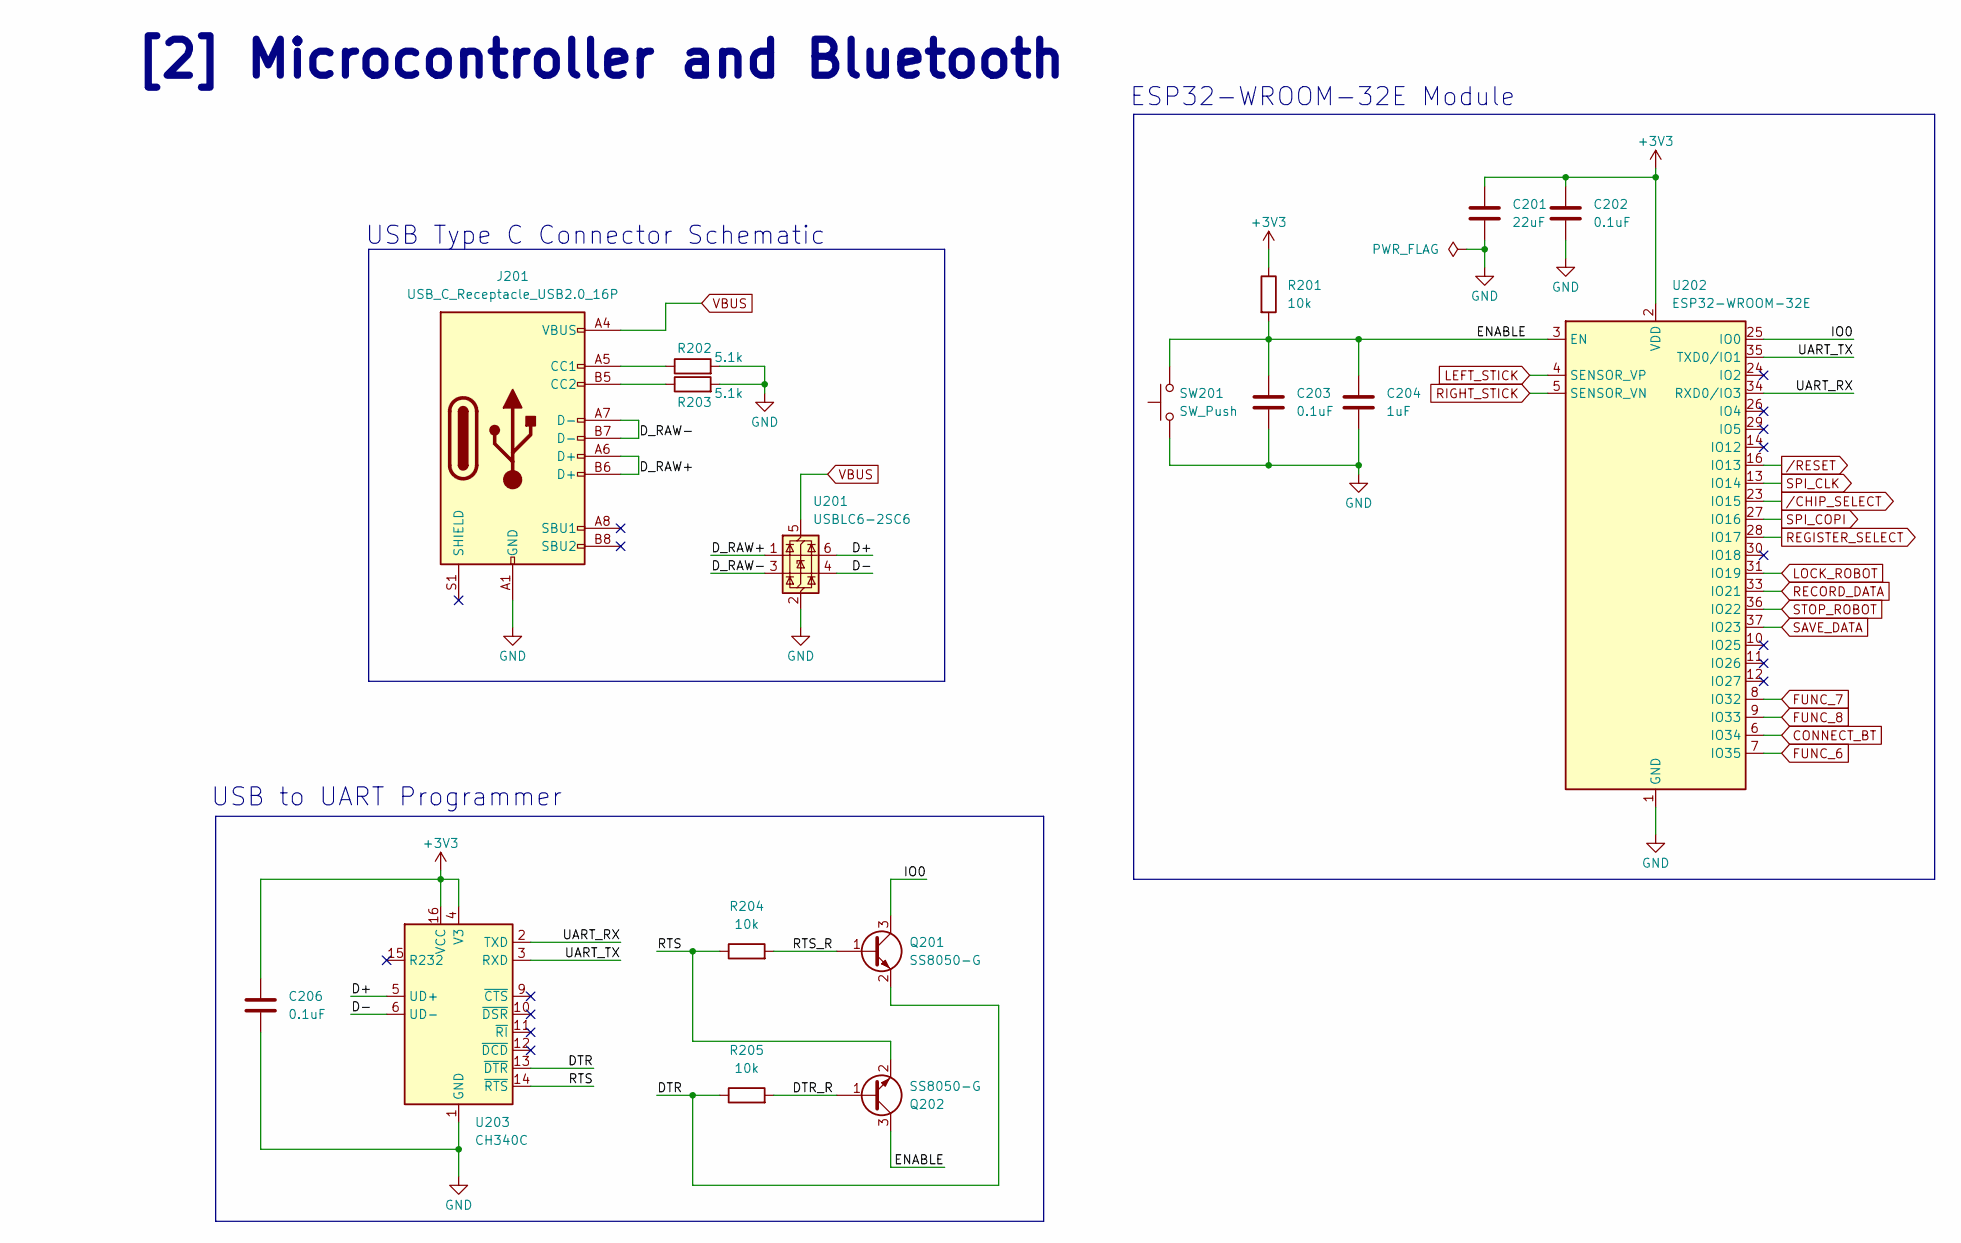
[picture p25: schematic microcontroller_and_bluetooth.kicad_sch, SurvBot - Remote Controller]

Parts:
C201: 22uF; C_0603_1608Metric; Manufacturer Part # CL10A226MQ8NRNC; JLCPCB Part # C59461
C202, C203, C206: 0.1uF; C_0402_1005Metric; Manufacturer Part # CL05B104KA5NNNC; JLCPCB Part # C155422
C204: 1uF; C_0402_1005Metric; Manufacturer Part # CL05A105KP5NNNC; JLCPCB Part # C14445
J201: USB_C_Receptacle_USB2.0_16P; USB_C_Receptacle_GCT_USB4105-xx-A_16P_TopMnt_Horizontal; Manufacturer Part # TYPE-C-31-M-12; JLCPCB Part # C165948
Q201, Q202: SS8050-G; SOT-23; Manufacturer Part # SS8050-G; JLCPCB Part # C3199946
R201, R204, R205: 10k; R_0402_1005Metric; Manufacturer Part # 0402WGJ0103TCE; JLCPCB Part # C25531
R202, R203: 5.1k; R_0603_1608Metric; Manufacturer Part # 0603WAF5101T5E; JLCPCB Part # C23186
SW201: SW_Push; SW_Tactile_SPST_NO_Straight_CK_PTS636Sx25SMTRLFS; Manufacturer Part # PTS636SK25SMTRLFS; JLCPCB Part # C2689642
U201: USBLC6-2SC6; SOT-23-6; Manufacturer Part # USBLC6-2SC6; JLCPCB Part # C7519
U202: ESP32-WROOM-32E; ESP32-WROOM-32D; Manufacturer Part # ESP32-WROOM-32E-N4; JLCPCB Part # C701341
U203: CH340C; SOIC-16_3.9x9.9mm_P1.27mm; Manufacturer Part # CH340C; JLCPCB Part # C84681

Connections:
+3V3: C201.1, C202.1, C206.1, R201.1, U202.2 (VDD), U203.4 (V3), U203.16 (VCC); also elsewhere on the board
/[2] Microcontroller And Bluetooth/D+: U201.6 (I/O1), U203.5 (UD+)
/[2] Microcontroller And Bluetooth/D-: U201.4 (I/O2), U203.6 (UD-)
/[2] Microcontroller And Bluetooth/DTR: Q201.2 (E), R205.1, U203.13 (~DTR)
/[2] Microcontroller And Bluetooth/DTR_R: Q202.1 (B), R205.2
/[2] Microcontroller And Bluetooth/D_RAW+: J201.A6 (D+), J201.B6 (D+), U201.1 (I/O1)
/[2] Microcontroller And Bluetooth/D_RAW-: J201.A7 (D-), J201.B7 (D-), U201.3 (I/O2)
/[2] Microcontroller And Bluetooth/ENABLE: C203.1, C204.1, Q202.3 (C), R201.2, SW201.2, U202.3 (EN)
/[2] Microcontroller And Bluetooth/IO0: Q201.3 (C), U202.25 (IO0)
/[2] Microcontroller And Bluetooth/RTS: Q202.2 (E), R204.1, U203.14 (~RTS)
/[2] Microcontroller And Bluetooth/RTS_R: Q201.1 (B), R204.2
/[2] Microcontroller And Bluetooth/UART_RX: U202.34 (RXD0/IO3), U203.2 (TXD)
/[2] Microcontroller And Bluetooth/UART_TX: U202.35 (TXD0/IO1), U203.3 (RXD)
CONNECT_BT: U202.6 (IO34); also elsewhere on the board
FUNC_6: U202.7 (IO35); also elsewhere on the board
FUNC_7: U202.8 (IO32); also elsewhere on the board
FUNC_8: U202.9 (IO33); also elsewhere on the board
GND: C201.2, C202.2, C203.2, C204.2, C206.2, J201.A1 (GND), J201.A12 (GND), J201.B1 (GND), J201.B12 (GND), R202.2, R203.2, SW201.1, U201.2 (GND), U202.1 (GND), U202.15 (GND), U202.38 (GND), U202.39 (GND), U203.1 (GND); also elsewhere on the board
LEFT_STICK: U202.4 (SENSOR_VP); also elsewhere on the board
LOCK_ROBOT: U202.31 (IO19); also elsewhere on the board
unnamed: J201.A5 (CC1), R202.1
unnamed: J201.B5 (CC2), R203.1
RECORD_DATA: U202.33 (IO21); also elsewhere on the board
REGISTER_SELECT: U202.28 (IO17); also elsewhere on the board
RIGHT_STICK: U202.5 (SENSOR_VN); also elsewhere on the board
SAVE_DATA: U202.37 (IO23); also elsewhere on the board
SPI_CLK: U202.13 (IO14); also elsewhere on the board
SPI_COPI: U202.27 (IO16); also elsewhere on the board
STOP_ROBOT: U202.36 (IO22); also elsewhere on the board
VBUS: J201.A4 (VBUS), J201.A9 (VBUS), J201.B4 (VBUS), J201.B9 (VBUS), U201.5 (VBUS); also elsewhere on the board
/CHIP_SELECT: U202.23 (IO15); also elsewhere on the board
/RESET: U202.16 (IO13); also elsewhere on the board

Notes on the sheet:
ESP32-WROOM-32E Module
[2] Microcontroller and Bluetooth
USB to UART Programmer
USB Type C Connector Schematic

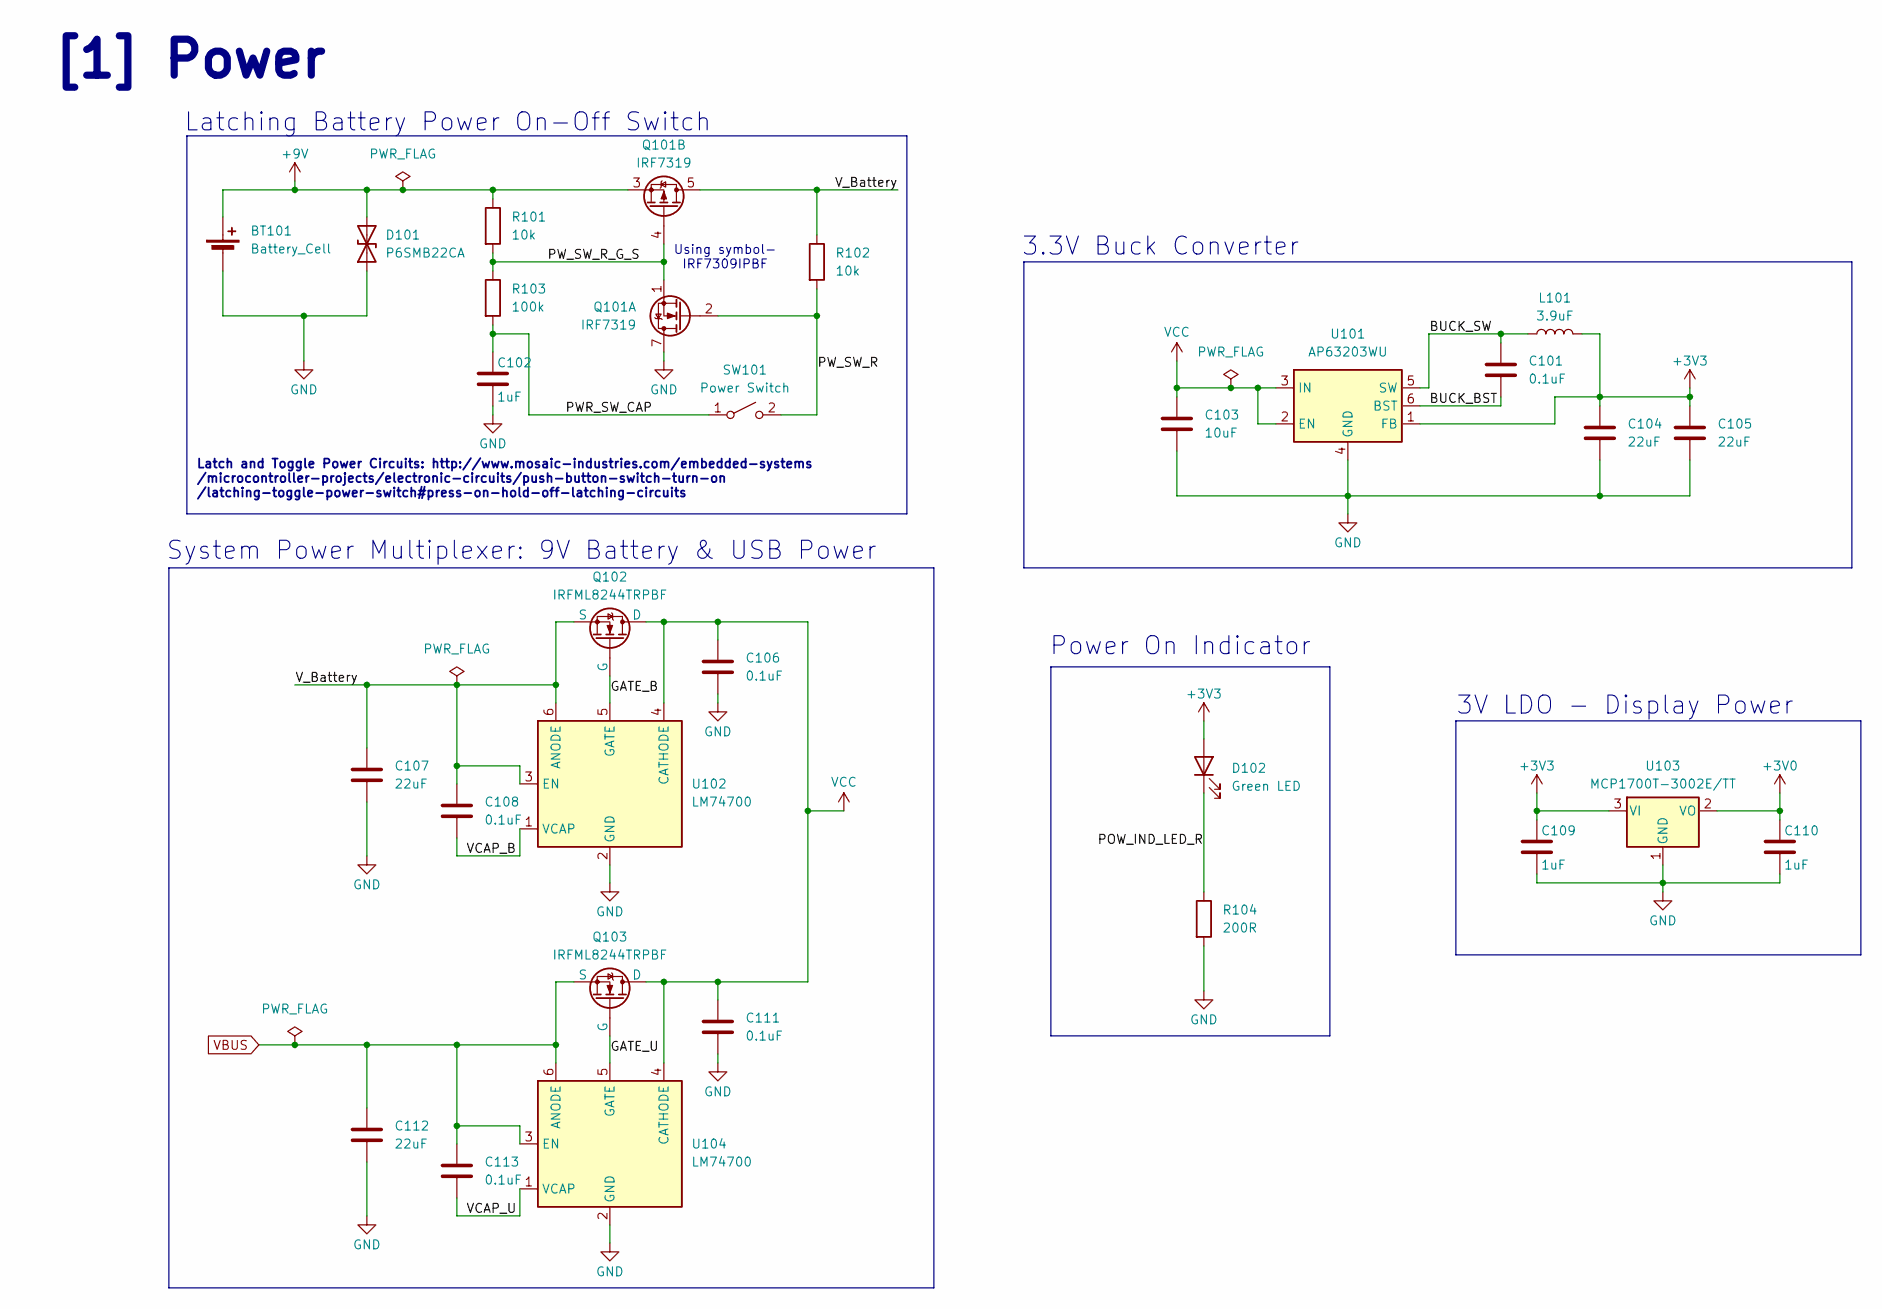
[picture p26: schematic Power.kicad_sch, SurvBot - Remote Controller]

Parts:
BT101: Battery_Cell; BatteryHolder_MPD_BA9VPC_1xPP3; Manufacturer Part # BA9VPC
C101, C106, C108, C111, C113: 0.1uF; C_0402_1005Metric; Manufacturer Part # CL05B104KA5NNNC; JLCPCB Part # C155422
C102, C109, C110: 1uF; C_0402_1005Metric; Manufacturer Part # CL05A105KP5NNNC; JLCPCB Part # C14445
C103: 10uF; C_0805_2012Metric; Manufacturer Part # GRM21BR61E106KA73L; JLCPCB Part # C84416
C104, C105, C107, C112: 22uF; C_1206_3216Metric; Manufacturer Part # GRM31CR61E226KE15L; JLCPCB Part # C77091
D101: P6SMB22CA; D_SOD-882; Manufacturer Part # P6SMB22CA; JLCPCB Part # C320520
D102: Green LED; LED_0603_1608Metric; Manufacturer Part # 150060GS75000; JLCPCB Part # C5252984
L101: 3.9uF; L_Vishay_IHLP-2525; Manufacturer Part # SQH6012S-4R0N-LF; JLCPCB Part # C257229
Q101: IRF7319; SOIC-8_3.9x4.9mm_P1.27mm; Manufacturer Part # IRF7319TRPBF; JLCPCB Part # C2760082
Q102, Q103: IRFML8244TRPBF; SOT-23; Manufacturer Part # IRFML8244TRPBF; JLCPCB Part # C5381404
R101, R102: 10k; R_0402_1005Metric; Manufacturer Part # 0402WGJ0103TCE; JLCPCB Part # C25531
R103: 100k; R_0603_1608Metric; Manufacturer Part # RC0603FR-07100KL; JLCPCB Part # C14675
R104: 200R; R_0603_1608Metric; Manufacturer Part # 0603WAF2000T5E; JLCPCB Part # C8218
SW101: Power Switch; SW_Push_1P1T_NO_CK_PTS125Sx43PSMTR; Manufacturer Part # TS-1003ST-26; JLCPCB Part # C455234
U101: AP63203WU; TSOT-23-6; Manufacturer Part # C780769; JLCPCB Part # AP63203WU-7
U102, U104: LM74700; SOT-23-6; Manufacturer Part # LM74700QDBVRQ1; JLCPCB Part # C2941042
U103: MCP1700T-3002E/TT; SOT-23; Manufacturer Part # MCP1700T-3002E/TT; JLCPCB Part # C62244

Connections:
+3V0: C110.1, U103.2 (VO); also elsewhere on the board
+3V3: C104.1, C105.1, C109.1, D102.2 (A), L101.2, U101.1 (FB), U103.3 (VI); also elsewhere on the board
+9V: BT101.1 (+), D101.2 (A2), Q101.3 (1), R101.1
/[1] Power/BUCK_BST: C101.2, U101.6 (BST)
/[1] Power/BUCK_SW: C101.1, L101.1, U101.5 (SW)
/[1] Power/GATE_B: Q102.1 (G), U102.5 (GATE)
/[1] Power/GATE_U: Q103.1 (G), U104.5 (GATE)
/[1] Power/POW_IND_LED_R: D102.1 (K), R104.1
/[1] Power/PWR_SW_CAP: C102.1, R103.2, SW101.1 (A)
/[1] Power/PW_SW_R: Q101.2 (G), R102.2, SW101.2 (B)
/[1] Power/PW_SW_R_G_S: Q101.1 (S), Q101.4 (G), R101.2, R103.1
/[1] Power/VCAP_B: C108.2, U102.1 (VCAP)
/[1] Power/VCAP_U: C113.2, U104.1 (VCAP)
/[1] Power/V_Battery: C107.1, C108.1, Q101.5 (D), Q101.6 (D), Q102.2 (S), R102.1, U102.3 (EN), U102.6 (ANODE)
GND: BT101.2 (-), C102.2, C103.2, C104.2, C105.2, C106.2, C107.2, C109.2, C110.2, C111.2, C112.2, D101.1 (A1), Q101.7 (D), Q101.8 (D), R104.2, U101.4 (GND), U102.2 (GND), U103.1 (GND), U104.2 (GND); also elsewhere on the board
VBUS: C112.1, C113.1, Q103.2 (S), U104.3 (EN), U104.6 (ANODE); also elsewhere on the board
VCC: C103.1, C106.1, C111.1, Q102.3 (D), Q103.3 (D), U101.2 (EN), U101.3 (IN), U102.4 (CATHODE), U104.4 (CATHODE)

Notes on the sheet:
[1] Power
Latching Battery Power On-Off Switch
3.3V Buck Converter
Power On Indicator
3V LDO - Display Power
Using symbol- IRF7309IPBF
System Power Multiplexer: 9V Battery & USB Power
Latch and Toggle Power Circuits: http://www.mosaic-industries.com/embedded-systems /microcontroller-projects/electronic-circuits/push-button-switch-turn-on /latching-toggle-power-switch#press-on-hold-off-latching-circuits

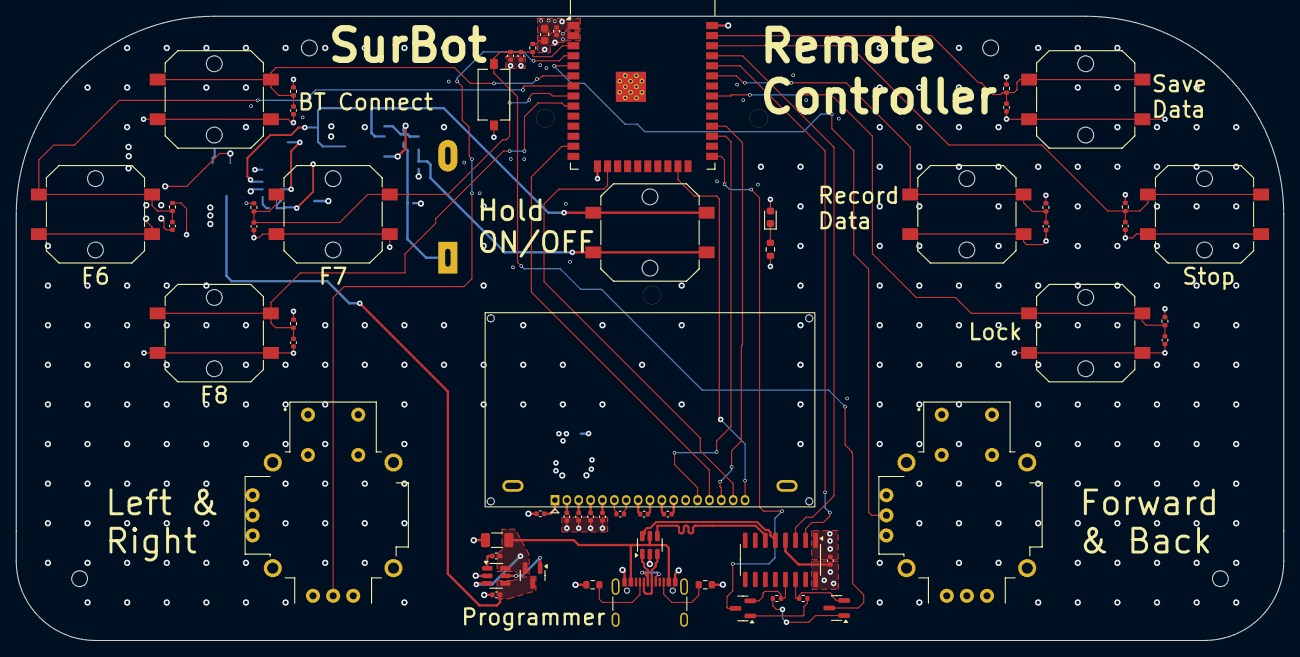
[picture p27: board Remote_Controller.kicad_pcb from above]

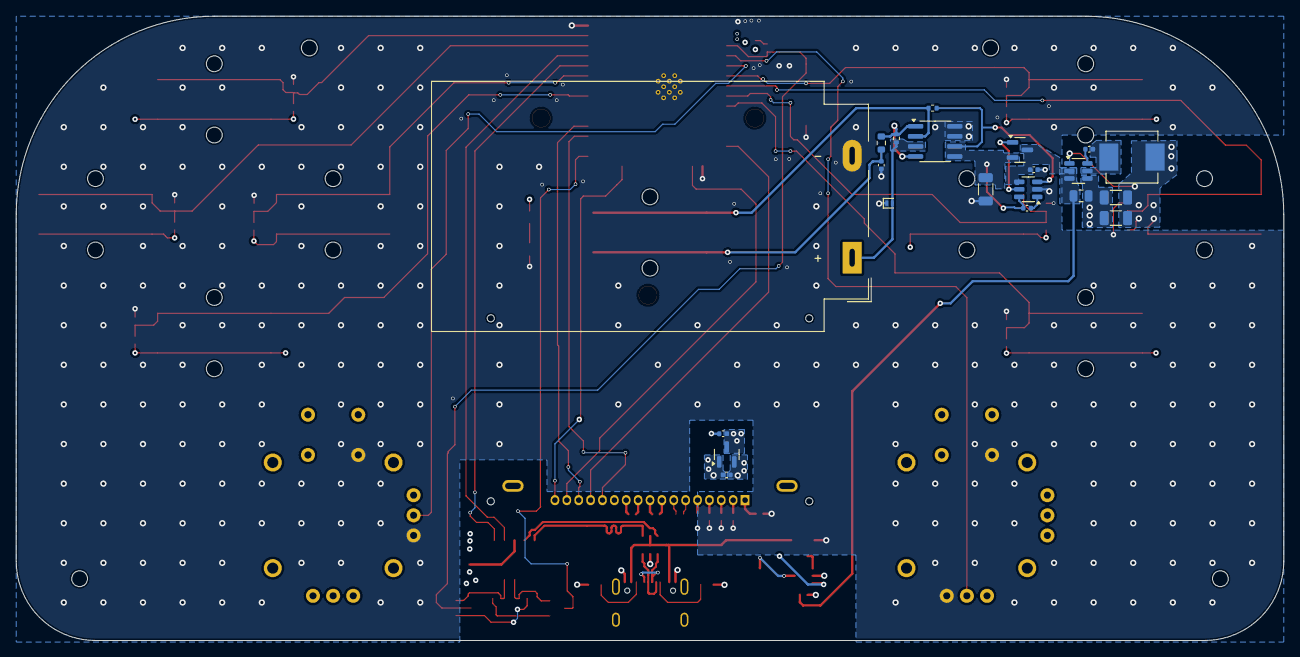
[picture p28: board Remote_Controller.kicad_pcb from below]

Board: 4 copper layers, 160.0 x 78.8 mm, 85 parts (21 on the bottom side), 56 nets.

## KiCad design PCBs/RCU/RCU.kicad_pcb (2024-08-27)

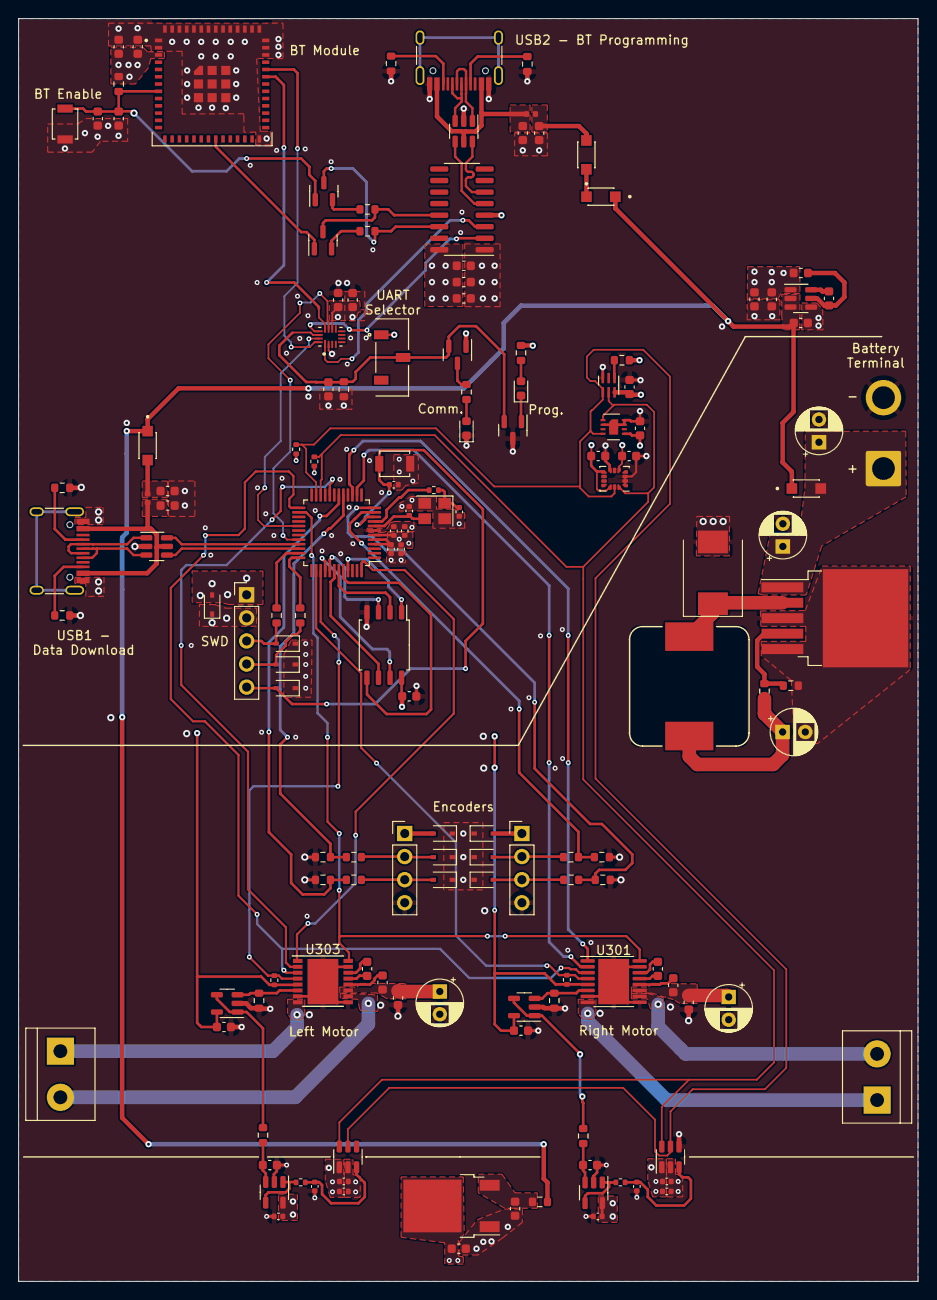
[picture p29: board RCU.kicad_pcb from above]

Board: 4 copper layers, 99.0 x 139.0 mm, 148 parts (0 on the bottom side), 98 nets.

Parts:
C100: 470u; CP_Radial_D5.0mm_P2.50mm
C101: 100uF; CP_Radial_D5.0mm_P2.50mm
C102: 1000uF; CP_Radial_D5.0mm_P2.50mm
C103, C400: 10uF; C_0603_1608Metric
C104: 100nF; C_0603_1608Metric
C105, C106, C109, C110, C404: 22uF; C_0603_1608Metric
C107, C108, C111, C112, C406, C500, C700: 1uF; C_0603_1608Metric
C200: 1uF; C_0402_1005Metric
C201, C203, C206, C600, C602, C605, C607: 0.1uF; C_0402_1005Metric
C202: 4.7uF; C_0402_1005Metric
C204, C205: 14pF; C_0402_1005Metric
C300, C302, C303, C305, C307, C308, C401, C402, C403, C405, C409, C501, C502, C504, C604, C609: 0.1uF; C_0603_1608Metric
C301, C306: 220uF; CP_Radial_D5.0mm_P2.50mm
C304, C309: 22nF; C_0603_1608Metric
C407: 1u; C_0603_1608Metric
C408: 0.1u; C_0603_1608Metric
C601, C606: 10uF; C_0402_1005Metric
C603, C608: 1nF; C_0402_1005Metric
D100: B340; D_SMC
D101, D102, D103, D104: SM5817; SODFL3719X135N
D200, D201, D202, D203, D300, D301, D302, D303, D304, D305: PESD3V3L1BA,115; D_SOD-323
D405: Green LED; LED_0603_1608Metric
D406: Blue LED; LED_0603_1608Metric
J100: Conn_01x02; SolderWire-2sqmm_1x02_P7.8mm_D2mm_OD3.9mm
J200, J400: USB_C_Receptacle_USB2.0; USB_C_Receptacle_HRO_TYPE-C-31-M-12
J201: Conn_01x05; PinHeader_1x05_P2.54mm_Vertical
J300: Right_Motor_Screw_Terminal; TerminalBlock_bornier-2_P5.08mm
J301: Right_Encoder_Conn; PinHeader_1x04_P2.54mm_Vertical
J302: Left_Motor_Screw_Terminal; TerminalBlock_bornier-2_P5.08mm
J303: Left_Encoder_Conn; PinHeader_1x04_P2.54mm_Vertical
L100: 68uH; IND_MWSA1206S_SNL
L101: 15uH; L_0603_1608Metric
L102, L103: 3.9uH; L_0402_1005Metric
Q400, Q401, Q403: 2N7002NXAKR (NMOS); SOT-23
Q402: BSS84AK,215 (PMOS); SOT-23
R100: 8.9k; R_0603_1608Metric
R101: 1.5k; R_0603_1608Metric
R102: 5R; R_0603_1608Metric
R200: 0R; R_0402_1005Metric
R201, R202, R300, R306: 10k; R_0402_1005Metric
R205, R206, R400, R401: 5.1k; R_0603_1608Metric
R207, R208: 49R9; R_0603_1608Metric
R301, R307: 2.2k; R_0603_1608Metric
R302, R303, R308, R309: 20k; R_0603_1608Metric
R304, R305, R310, R311: 40k; R_0603_1608Metric
R402, R403, R404, R405, R500: 10k; R_0603_1608Metric
R406: 40R; R_0603_1608Metric
R407: 110R; R_0603_1608Metric
R600, R607: 15R; R_0402_1005Metric
R601, R603: 1.6k; R_0603_1608Metric
SW201, SW400: SW_Push; SW_SPST_B3U-1000P
SW401: SW_SPDT; SW_JS102011JCQN
U100: LM2576S-ADJ; TO-263-5_TabPin3
U101: AP63203WU; TSOT-23-6
U102: AZ1117-3.3; TO-252-2
U200: STM32G0B1CBT6; LQFP-48_7x7mm_P0.5mm
U201, U400: USBLC6-2SC6; SOT-23-6
U300, U302, U601, U603: OPA320; SOT-23-5
U301: DRV8876; HTSSOP-16-1EP_4.4x5mm_P0.65mm_EP3.4x5mm_Mask2.46x2.31mm
U303: DRV8876; HTSSOP-16-1EP_4.4x5mm_P0.65mm_EP3.4x5mm
U401: CH340C; SOP-16_3.9x9.9mm_P1.27mm
U402: ESP32-MINI-1; XCVR_ESP32-MINI-1-N4
U403: DG2788ADN-T1-GE4; QFN40P260X180X55-16N
U500: APDS-9306-065; Broadcom_DFN-6_2x2mm_P0.65mm
U501: LSM6DS3; LGA-14_3x2.5mm_P0.5mm_LayoutBorder3x4y
U502: SHT30-DIS; Sensirion_DFN-8-1EP_2.5x2.5mm_P0.5mm_EP1.1x1.7mm
U600, U602: ADC121C027CIMK/NOPB; TSOT-23-6
U700: SST26VF032BT-104I/SM; SOIC-8_5.275x5.275mm_P1.27mm
Y200: 16MHz; Crystal_SMD_3225-4Pin_3.2x2.5mm

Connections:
+3.3VA: C110.1, C600.2, C601.1, C602.1, C605.2, C606.1, C607.1, U102.2 (VO), U600.1 (VA), U601.5 (V+), U602.1 (VA), U603.5 (V+)
+3V3: C105.1, C106.1, C200.1, C201.1, C202.1, C203.1, C302.1, C307.1, C400.1, C401.1, C402.1, C403.1, C404.1, C407.1, C408.1, C500.1, C501.2, C502.2, C504.1, C700.2, D200.2 (A2), J201.1, L101.2, Q402.1 (D), R201.2, R202.2, R300.1, R306.2, R404.2, R407.1, R500.1, SW401.1 (A), U101.1 (FB), U200.4 (VBAT), U200.5 (VREF+), U200.6 (VDD/VDDA), U300.5 (V+), U301.5 (VREF), U302.5 (V+), U303.5 (VREF), U401.4 (V3), U401.16 (VCC), U402.3 (3V3), U403.10 (V+), U500.3 (VDD), U501.5 (VDDIO), U501.8 (VDD), U501.12 (CS), U502.5 (VDD), U700.8 (VDD)
+5C: C108.1, D102.2 (A), L102.2
+5F: C112.1, D103.2 (A), L103.2
+6V: C102.1, C300.1, C301.1, C303.1, C305.1, C306.1, C308.1, D302.2 (A2), D305.2 (A2), J301.1, J303.1, L100.2, R100.2, U301.11 (VM), U303.11 (VM)
+BATT: C100.1, C101.1, D101.2 (A), J100.1, U100.1 (VIN)
/[1] Power/BATT_FILT: C109.1, R102.2, U102.3 (VI)
/[1] Power/BOOST_IN_104: C104.1, U101.6 (BST)
/[1] Power/BUCK_FB_104: R100.1, R101.2, U100.4 (FB)
/[1] Power/BUCK_OUT_104: D100.1 (K), L100.1, U100.2 (OUT)
/[1] Power/SWO_100: C104.2, L101.1, U101.5 (SW)
/[2] Microcontroller/CC1: J200.A5 (CC1), R205.1
/[2] Microcontroller/CC2: J200.B5 (CC2), R206.2
/[2] Microcontroller/D+: J200.A6 (D+), J200.B6 (D+), U201.3 (I/O2)
/[2] Microcontroller/D-: J200.A7 (D-), J200.B7 (D-), U201.1 (I/O1)
/[2] Microcontroller/HSE_IN: C204.1, U200.8 (PF0-OSC_IN), Y200.3
/[2] Microcontroller/HSE_OUT: R200.2, U200.9 (PF1-OSC_OUT)
/[2] Microcontroller/NRST: C206.1, D203.2 (A2), J201.5, SW201.2, U200.10 (PF2-NRST)
/[2] Microcontroller/Prot_D+: U200.34 (PA12[PA10]), U201.4 (I/O2)
/[2] Microcontroller/Prot_D-: U200.33 (PA11[PA9]), U201.6 (I/O1)
/[2] Microcontroller/SWCLK: D202.2 (A2), J201.4, R208.1
/[2] Microcontroller/SWCLK_Pin: R208.2, U200.36 (PA14-BOOT0)
/[2] Microcontroller/SWDIO: D201.2 (A2), J201.3, R207.1
/[2] Microcontroller/SWDIO_Pin: R207.2, U200.35 (PA13)
/[3] Motor_Control/6V_LeftA_Output: D304.2 (A2), J303.2, R308.2
/[3] Motor_Control/6V_LeftB_Output: D303.2 (A2), J303.3, R309.2
/[3] Motor_Control/6V_RightA_Output: D301.2 (A2), J301.2, R302.2
/[3] Motor_Control/6V_RightB_Output: D300.2 (A2), J301.3, R303.2
/[3] Motor_Control/LEFT_CPH: C309.1, U303.13 (CPH)
/[3] Motor_Control/LEFT_CPL: C309.2, U303.14 (CPL)
/[3] Motor_Control/LEFT_CP_OUTPUT: C308.2, U303.12 (VCP)
/[3] Motor_Control/Left_Out1: J302.1, U303.8 (OUT1)
/[3] Motor_Control/Left_Out2: J302.2, U303.10 (OUT2)
/[3] Motor_Control/Left_Sensed_Motor_Current: R307.1, U302.3 (+), U303.6 (IPROPI)
/[3] Motor_Control/RIGHT_CPH: C304.1, U301.13 (CPH)
/[3] Motor_Control/RIGHT_CPL: C304.2, U301.14 (CPL)
/[3] Motor_Control/RIGHT_CP_OUTPUT: C303.2, U301.12 (VCP)
/[3] Motor_Control/Right_Out1: J300.1, U301.8 (OUT1)
/[3] Motor_Control/Right_Out2: J300.2, U301.10 (OUT2)
/[3] Motor_Control/Right_Sensed_Motor_Current: R301.1, U300.3 (+), U301.6 (IPROPI)
/[4] Bluetooth/BT_D+: U400.4 (I/O2), U401.5 (UD+)
/[4] Bluetooth/BT_D-: U400.6 (I/O1), U401.6 (UD-)
/[4] Bluetooth/BT_EN: C405.1, C406.1, Q401.1 (D), R404.1, SW400.2, U402.8 (EN)
/[4] Bluetooth/BT_Raw_D+: J400.A6 (D+), J400.B6 (D+), U400.3 (I/O2)
/[4] Bluetooth/BT_Raw_D-: J400.A7 (D-), J400.B7 (D-), U400.1 (I/O1)
/[4] Bluetooth/CC1: J400.A5 (CC1), R400.1
/[4] Bluetooth/CC2: J400.B5 (CC2), R401.2
/[4] Bluetooth/DTR: Q400.3 (S), R403.1, U401.13 (~DTR)
/[4] Bluetooth/DTR_R: Q401.2 (G), R403.2
/[4] Bluetooth/IO0: Q400.1 (D), U402.21 (IO0)
/[4] Bluetooth/RTS: Q401.3 (S), R402.1, U401.14 (~RTS)
/[4] Bluetooth/RTS_R: Q400.2 (G), R402.2
/[4] Bluetooth/UART_SELECT: C409.1, Q402.2 (G), Q403.2 (G), R405.1, SW401.2 (B), U403.14 (IN1-2)
/[5] Sensors/Light_sensor INT_H: R500.2, U500.4 (INT)
/[6] ADCs/ADC_LEFT_IN: C603.1, R600.1, U600.3 (VIN)
/[6] ADCs/ADC_RIGHT_IN: C608.1, R607.1, U602.3 (VIN)
/[6] ADCs/LEFT_AMP_OUT: R607.2, U603.1, U603.4 (-)
/[6] ADCs/RIGHT_AMP_OUT: R600.2, U601.1, U601.4 (-)
Awake_Sleep: U200.25 (PB13), U301.3 (nSLEEP), U303.3 (nSLEEP)
Buffered_Left_Sensed_Motor_Current: R603.2, U302.1, U302.4 (-)
Buffered_Right_Sensed_Motor_Current: R601.2, U300.1, U300.4 (-)
Control_Input_Mode: U200.26 (PB14), U301.16 (PMODE), U303.16 (PMODE)
GND: C100.2, C101.2, C102.2, C103.2, C105.2, C106.2, C107.2, C108.2, C109.2, C110.2, C111.2, C112.2, C200.2, C201.2, C202.2, C203.2, C204.2, C205.1, C206.2, C300.2, C301.2, C302.2, C305.2, C306.2, C307.2, C400.2, C401.2, C402.2, C403.2, C404.2, C405.2, C406.2, C407.2, C408.2, C409.2, C500.2, C501.1, C502.1, C504.2, C600.1, C601.2, C602.2, C603.2, C604.1, C605.1, C606.2, C607.2, C608.2, C609.1, C700.1, D100.2 (A), D200.1 (A1), D201.1 (A1), D202.1 (A1), D203.1 (A1), D300.1 (A1), D301.1 (A1), D302.1 (A1), D303.1 (A1), D304.1 (A1), D305.1 (A1), D405.1 (K), J100.2, J200.A1 (GND), J200.A12 (GND), J200.B1 (GND), J200.B12 (GND), J201.2, J301.4, J303.4, J400.A1 (GND), J400.A12 (GND), J400.B1 (GND), J400.B12 (GND), Q403.3 (S), R101.1, R205.2, R206.1, R301.2, R304.1, R305.1, R307.2, R310.1, R311.1, R400.2, R401.1, R405.2, SW201.1, SW400.1, U100.3 (GND), U100.5 (~ON/OFF), U101.4 (GND), U102.1 (GND), U200.7 (VSS/VSSA), U201.2 (GND), U300.2 (V-), U301.7 (IMODE), U301.9 (PGND), U301.15 (GND), U301.17 (pad), U302.2 (V-), U303.7 (IMODE), U303.9 (PGND), U303.15 (GND), U303.17 (pad), U400.2 (GND), U401.1 (GND), U402.1 (GND), U402.2 (GND), U402.27 (GND), U402.38 (GND), U402.39 (GND), U402.40 (GND), U402.41 (GND), U402.42 (GND), U402.43 (GND), U402.44 (GND), U402.45 (GND), U402.46 (GND), U402.47 (GND), U402.48 (GND), U402.49 (GND), U402.50 (GND), U402.51 (GND), U402.52 (GND), U402.53 (GND), U402.54 (GND), U402.55 (GND), U403.2 (GND), U500.6 (GND), U501.1 (SDO/SA0), U501.2 (SDX), U501.3 (SCX), U501.7 (GND), U502.2 (ADDR), U502.7 (R), U502.8 (VSS), U502.9 (VSS), U600.2 (GND), U600.4 (ADDR), U601.2 (V-), U602.2 (GND), U603.2 (V-), U700.4 (VSS), Y200.2, Y200.4
Hold: U200.40 (PD2), U700.7 (~HOLD)
I2C_SCL: R201.1, U200.23 (PB11), U500.1 (SCL), U501.13 (SCL), U502.4 (SCL), U600.5 (SCL), U602.5 (SCL)
I2C_SDA: R202.1, U200.22 (PB10), U500.2 (SDA), U501.14 (SDA), U502.1 (SDA), U600.6 (SDA), U602.6 (SDA)
Left_Enable/PWM: U200.48 (PB9), U303.1 (EN/IN1)
Left_Phase/PWM: U200.20 (PB1), U303.2 (PH/IN2)
Left_Wheel_Encoder_A: R308.1, R310.2, U200.17 (PA6)
Left_Wheel_Encoder_B: R309.1, R311.2, U200.18 (PA7)
Mem_Select: U200.45 (PB6), U700.1 (~CE)
unnamed: C205.2, R200.1, Y200.1
unnamed: C604.2, R601.1, U601.3 (+)
unnamed: C609.2, R603.1, U603.3 (+)
unnamed: D103.1 (K), D104.2 (A)
unnamed: D405.2 (A), R406.2
unnamed: D406.1 (K), Q403.1 (D)
unnamed: D406.2 (A), R407.2
unnamed: Q402.3 (S), R406.1
Right_Enable/PWM: U200.15 (PA4), U301.1 (EN/IN1)
Right_Phase/PWM: U200.14 (PA3), U301.2 (PH/IN2)
Right_Wheel_Encoder_A: R302.1, R304.2, U200.11 (PA0)
Right_Wheel_Encoder_B: R303.1, R305.2, U200.12 (PA1)
SPI_MISO: U200.43 (PB4), U700.2 (SO)
SPI_MOSI: U200.44 (PB5), U700.5 (SI)
SPI_SCK: U200.42 (PB3), U700.6 (SCK)
UART_BT_RX: U402.35 (RXD0), U403.12 (COM1)
UART_BT_TX: U402.36 (TXD0), U403.16 (COM2)
UART_MCU_RX: U200.29 (PA9), U403.15 (NO2)
UART_MCU_TX: U200.32 (PA10), U403.11 (NO1)
UART_PGR_RX: U401.3 (RXD), U403.1 (NC2)
UART_PGR_TX: U401.2 (TXD), U403.13 (NC1)
VBUS1: C107.1, J200.A4 (VBUS), J200.A9 (VBUS), J200.B4 (VBUS), J200.B9 (VBUS), L102.1, U201.5 (VBUS)
VBUS2: C111.1, J400.A4 (VBUS), J400.A9 (VBUS), J400.B4 (VBUS), J400.B9 (VBUS), L103.1, U400.5 (VBUS)
VCOM: C103.1, D101.1 (K), D102.1 (K), D104.1 (K), R102.1, U101.2 (EN), U101.3 (IN)
Write_Protect: U200.41 (PD3), U700.3 (~WP)
nFault_Left: R306.1, U200.39 (PD1), U303.4 (nFAULT)
nFault_Right: R300.2, U200.38 (PD0), U301.4 (nFAULT)

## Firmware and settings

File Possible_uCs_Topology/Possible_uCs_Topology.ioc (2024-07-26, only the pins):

Mcu.UserName=STM32G0B1CBTx
PA0.GPIO_Label=Right_Wheel_Encoder_A
PA0.Signal=S_TIM2_CH1_ETR
PA1.GPIO_Label=Right_Wheel_Encoder_B
PA1.Signal=S_TIM2_CH2
PA10.Signal=USART1_RX
PA13.Signal=SYS_SWDIO
PA14-BOOT0.Signal=SYS_SWCLK
PA3.GPIO_Label=Right_Phase/PWM
PA3.Signal=S_TIM2_CH4
PA4.GPIO_Label=Right_Enable/PWM
PA4.Signal=S_TIM14_CH1
PA6.GPIO_Label=Left_Wheel_Encoder_A
PA6.Signal=S_TIM3_CH1
PA7.GPIO_Label=Right_Wheel_Encoder_B
PA7.Signal=S_TIM3_CH2
PA9.Signal=USART1_TX
PB1.GPIO_Label=Left_Phase/PWM
PB1.Signal=S_TIM3_CH4
PB10.Signal=I2C2_SCL
PB11.Signal=I2C2_SDA
PB13.GPIO_Label=Awake_Sleep
PB13.Signal=GPIO_Output
PB14.GPIO_Label=Control_Input_Mode
PB14.Signal=GPIO_Output
PB3.Signal=SPI3_SCK
PB4.Signal=SPI3_MISO
PB5.Signal=SPI3_MOSI
PB9.GPIO_Label=Left_Enable/PWM
PB9.Signal=S_TIM4_CH4
PD0.GPIO_Label=nFault_Right
PD0.Signal=GPIO_Input
PD1.GPIO_Label=nFault_Left
PD1.Signal=GPIO_Input

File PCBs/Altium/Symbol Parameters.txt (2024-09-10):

Manufacturer
Manufacturer Part #
Case/Package
Supplier
Supplier Part #

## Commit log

2024-03-25 Bought materials needed for prototyping, chassis, motor, motor controllers, environment sensors
    [BOM.xlsx]
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2024-04-07 Can send speed commands to UART and correctly parse them
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2024-04-14 Corrected calcControl function prototype
2024-04-17 Corrected PID equation, add more information in MSG2, and corrected issue that caused motor to rotate at max speed at times
    Integral part of equation has to be multiplied by the time period, and in HAL_TIM_PeriodEleapsedCallback, the if statements that decide whether to try to rotate the wheel in the forward or reverse direction should be decided by the sign of the output control PWM signal of calcControl not the sign of of the velocity command sent over UART
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2024-04-19 Started Robot PCB schematic - RCU (Robot Control Unit
    Using STM32G0B1CBTC, imported the uC's design files (footprint, symbol and 3d file)
    [RCU.kicad_pcb, RCU.kicad_sch, microcontroller.kicad_sch]
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2024-06-02 Mapped out Motor Control, I2C, UART and USB pins on microcontroller, will be using STM32G0B1CBT6
    [microcontroller.kicad_sch]
2024-06-02 Updated microcontroller schematic and created motor_control schematic
    Changed all the net lables to global lavels except for NRST and USB_, added crystal resonator circuit, created DRV8876 symbol and added control signals to it
    [RCU.kicad_sch, microcontroller.kicad_sch, motor_control.kicad_sch]
2024-06-04 Completed connections and values for motor driver circuit
    [RCU.kicad_sch, microcontroller.kicad_sch, motor_control.kicad_sch]
2024-06-04 Add Awake_Sleep and Contro_Input_Mode pin assignments to uC
    [microcontroller.kicad_sch, motor_control.kicad_sch]
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2024-06-17 Added Pullup Resistors to SCL and SDA lines
    [RCU.kicad_sch, microcontroller.kicad_sch]
2024-06-17 Added ADC that will convert sensed motor currents to I2C
    [RCU.kicad_sch, microcontroller.kicad_sch, motor_control.kicad_sch]
2024-06-17 Prepended 'SDA' and 'SCL' global labels with 'I2C_'
    [motor_control.kicad_sch, sensors.kicad_sch]
2024-06-18 Added Encoder connector terminals for left and right motors
    [RCU.kicad_sch, microcontroller.kicad_sch, motor_control.kicad_sch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]
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2024-06-18 Decreased paper size for motor control schematic and corrected the name of op amp used in ADC
    [ADCs.kicad_sch, RCU.kicad_sch, motor_control.kicad_sch]
2024-06-28 Simulated how LPF and voltage buffer would affect current sensing reading
    [ADCs.kicad_sch, RCU.kicad_sch, motor_control.kicad_sch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]
2024-06-28 Add output buffer to IPROPI pin of Motor Driver ICs and low pass RC filter and input buffer to ADCs
    [ADCs.kicad_sch, RCU.kicad_sch, motor_control.kicad_sch]
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2024-07-02 Adding programming capability and starting power selector circuit
    [RCU.kicad_sch, bluetooth.kicad_sch, microcontroller.kicad_sch]
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2024-07-25 Microcontroller will take nFaults of both motor controllers as inputs
    [RCU.kicad_sch, microcontroller.kicad_sch, motor_control.kicad_sch]
2024-07-25 Added SPI ports to microconroller, to be used for external memory
    [microcontroller.kicad_sch]
2024-07-26 Add USB power filter circuitry and corrected Motor Driver schematic
    [Power.kicad_sch, RCU.kicad_sch, microcontroller.kicad_sch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]
2024-07-26 Add battery filter circuit, corrected cap values for 3.3V regulators, used different output power floag for Bottom regulator so that it only powers the Bluetooth susbsystem
    [Power.kicad_sch, RCU.kicad_sch, bluetooth.kicad_sch]
2024-07-26 Made corrections to Power module and power flag used to power BT susbsystem
    [Power.kicad_sch, RCU.kicad_sch]
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2024-07-26 Sectioned ADC module and corrected Motor current output name
    [ADCs.kicad_sch, motor_control.kicad_sch, sensors.kicad_sch]
2024-07-26 Changed internal numbering of Sensors schematic from 3 to 5
    [sensors.kicad_sch]
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2024-07-27 The shared SWCLK/BOOT0 pin has an internal pull-down resistor, and in the case where SWCLK is shared and are programming with SWD, just need NRST conncted to the STLink-V2 module
    [Power.kicad_sch, RCU.kicad_sch, bluetooth.kicad_sch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]
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2024-07-28 Added 16Mhz crystal oscillator, along with load capacitors and external resistor
    [RCU.kicad_sch, microcontroller.kicad_sch]
2024-07-29 Will use a 6V battery instead of 9V, since motor I am using is rated for 6V
    [Power.kicad_sch, RCU.kicad_sch, microcontroller.kicad_sch]
2024-07-30 Updated switching regulator inductor values and annotated 4th diode in power schematic
    [Power.kicad_sch, RCU.kicad_sch]
2024-07-31 Use Rext = 0 ohms for oscillator circuit
    [Power.kicad_sch, RCU.kicad_sch, microcontroller.kicad_sch]
2024-08-01 Simulated pi filter for getting rid of noise on USB power line, inductor ESR is 0.15 ohms
2024-08-01 Corrected cap values in regulators, changed voltage after battery filter to 9V, will use a 6V regulator to power motors in the near future
    [Power.kicad_sch, RCU.kicad_sch, microcontroller.kicad_sch]
2024-08-02 Corrected C302 and C305 values in motor drive units, should be 22nF, not 22uF
    [Power.kicad_sch, RCU.kicad_sch, motor_control.kicad_sch]
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2024-08-02 Replaced ADCs with ADC121C027, easy to program the addresses
    [ADCs.kicad_sch, RCU.kicad_sch]
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2024-08-05 Replaced Bidrectional TVS diodes with USBLC-2SC6 unidirectional ESD protection
    [RCU.kicad_sch, external_memory.kicad_sch, microcontroller.kicad_sch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]
2024-08-05 Added ESD protection to 3.3V pin of SWD connector, and made motor sheet larger
    [RCU.kicad_sch, microcontroller.kicad_sch, motor_control.kicad_sch]
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2024-08-10 Corrected resistor values for stepping down encoder output voltage
    [RCU.kicad_sch, microcontroller.kicad_sch, motor_control.kicad_sch]
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2024-08-10 Corrected ESP32-Mini bypass caps and added push-button reset circuit
    [RCU.kicad_sch, bluetooth.kicad_sch]
2024-08-10 Added bypass capacitors to IC switch, the datasheet did not recomend any
    [RCU.kicad_sch, bluetooth.kicad_sch]
2024-08-10 Replaced OPA365 op amps with OPA320 op amps
    [ADCs.kicad_sch, RCU.kicad_sch]
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2024-08-10 Updated ADC schematic to match application note in ADC and op-amp data sheets
    [ADCs.kicad_sch, RCU.kicad_sch, bluetooth.kicad_sch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]
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2024-08-11 Removed TVS diodes for motor terminals, label TVS diodes for encoder, using OPA320 op amps in motor control schematic, it is now fully annotated
    [RCU.kicad_sch, motor_control.kicad_sch]
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2024-08-11 Wrote that first regulator in power schematic also powers the external memory
    [Power.kicad_sch, bluetooth.kicad_sch, sensors.kicad_sch]
2024-08-11 Update README.md
    corrected power schematic and associated image
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2024-08-12 Corrected SPI_MOSI and SPI_MISO labels on U700 - external memory
    [ADCs.kicad_sch, Power.kicad_sch, bluetooth.kicad_sch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]
2024-08-12 Change address pin of left motor ADC to floating so that it and the light sensor will have diffeent addresses, wrote slave addresses for ADCs and light sensor
    [ADCs.kicad_sch, sensors.kicad_sch]
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2024-08-19 Add footprint to power module diodes, and replaced 1N4148W with 2 SM5817's
    [ADCs.kicad_sch, Power.kicad_sch, RCU.kicad_sch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]
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2024-08-20 Corrected symbol for U300 and U302
    [RCU.kicad_sch, motor_control.kicad_sch]
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2024-08-20 Corrected footprint for U200
    [RCU.kicad_pcb, RCU.kicad_sch, microcontroller.kicad_sch]
2024-08-20 USB2 can now power all modules except motor control if it is the only power source that is plugged in
    [ADCs.kicad_sch, Power.kicad_sch, RCU.kicad_sch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]
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2024-08-22 Added motor driver footrpint and replaced diode 1N5822 with B340AE-13
    [PWP0016C.stp, RCU.kicad_pcb, RCU.kicad_sch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]
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2024-08-23 changed pad clearance of uart selector to 0.1mm
    [RCU.kicad_pcb, RCU.kicad_sch, bluetooth.kicad_sch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]
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2024-08-27 Got rid of necessary errors and warnings
    [RCU.kicad_pcb]
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2024-09-08 Corrected R100 value, it is now 5.9k instead of 8.9k
    [Power.kicad_sch, RCU.kicad_sch, microcontroller.kicad_sch]
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2024-09-10 Corrected power rating of 5R1 resistor
    [1_SurvBot_RCU_Power.SchDoc, GhaniLibrary.SchLib]
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2024-09-12 Corrected op amp symbol
    [6_SurvBot_RCU_CurrentFeedback.SchDoc, GhaniLibrary.SchLib]
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2024-09-12 Took care of valid DRC errors and warnings
    [1_SurvBot_RCU_Power.SchDoc, 2_SurvBot_RCU_MCU.SchDoc, 3_SurvBot_RCU_MotorControl.SchDoc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]
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2024-09-14 Corrected ESP32-Mini footprint pin assignment
    [1_SurvBot_RCU_Power.SchDoc, 2_SurvBot_RCU_MCU.SchDoc, 3_SurvBot_RCU_MotorControl.SchDoc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]
2024-09-14 Corrected CONN 4P footprint pin assignment
    [3_SurvBot_RCU_MotorControl.SchDoc, GhaniLibrary.PcbLib, GhaniLibrary.SchLib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]
2024-09-14 Corrected TVS diode footprint pin assignment
    [3_SurvBot_RCU_MotorControl.SchDoc, GhaniLibrary.PcbLib, GhaniLibrary.SchLib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]
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2024-09-16 Add decoupling caps to ESP32and correct USB ESD correction connections
    [2_SurvBot_RCU_MCU.SchDoc, 4_SurvBot_RCU_Bluetooth.SchDoc]
2024-09-16 Corrected analog IC power pins and change BATT_FILT to VCOM_FILT
    [1_SurvBot_RCU_Power.SchDoc, GhaniLibrary.SchLib]
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2024-09-16 Add differential pair tags to Protected MCU and BT USB traces, and traced MCU USB net
    [2_SurvBot_RCU_MCU.SchDoc, 4_SurvBot_RCU_Bluetooth.SchDoc]
2024-09-16 Correctly connect BT enable in schematic
    [4_SurvBot_RCU_Bluetooth.SchDoc]
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2024-09-18 Updated rules, electrical issues appear to be solved, still have solder mask and silk issues, but they are low priority for now
    [GhaniLibrary.PcbLib, SurvBot-RCU.PrjPcb]
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2025-02-12 Add LCD screen symbol to project library, and add LCD screen and function buttons to user interface schematic
    [user_interface.kicad_sch]
2025-02-12 Add Power on indicator light, made small corrections
    [Power.kicad_sch, microcontroller_and_bluetooth.kicad_sch]
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2025-02-12 Corrected uC-screen connection names
    [microcontroller_and_bluetooth.kicad_sch, user_interface.kicad_sch]
2025-02-17 Added Thumb joystick symbols, and finish UI schematic with joysticks to control rotational and linear velocity
    [user_interface.kicad_sch]
2025-02-17 Labeled all nets, corrected some labels, added battery-cell symbol
    [Power.kicad_sch, microcontroller_and_bluetooth.kicad_sch, user_interface.kicad_sch]
2025-02-20 Added Buck converter with a reverse breakdown voltage that is much higher than the nominal input voltage, and added TVS diode
    [Power.kicad_sch]
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2025-02-22 Add Latching Power On-Off switch circuit - allows user to turn device on and off with a tactile switch
    [Power.kicad_sch, user_interface.kicad_sch]
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2025-02-24 Updated joystick symbol, correct Dual fet footprint and annotated news in power toggle circuit
    [Power.kicad_sch, Remote_Controller.kicad_pcb, user_interface.kicad_sch]
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2025-03-05 Finish rough layout, add 3D model of ESP32, pushbuttons, Display, tactile switch
    [Download_STP_430172073816_rev1.stp, ESP32-WROOM-32E-H4.STEP, NHD-C12832A1Z.STEP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]
2025-03-06 Reduced size of capacitor C201 to 0603 and corrected CH340 cap decoupler circuit, also improved PCB layout
    [Power.kicad_sch, Remote_Controller.kicad_pcb, microcontroller_and_bluetooth.kicad_sch]
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
